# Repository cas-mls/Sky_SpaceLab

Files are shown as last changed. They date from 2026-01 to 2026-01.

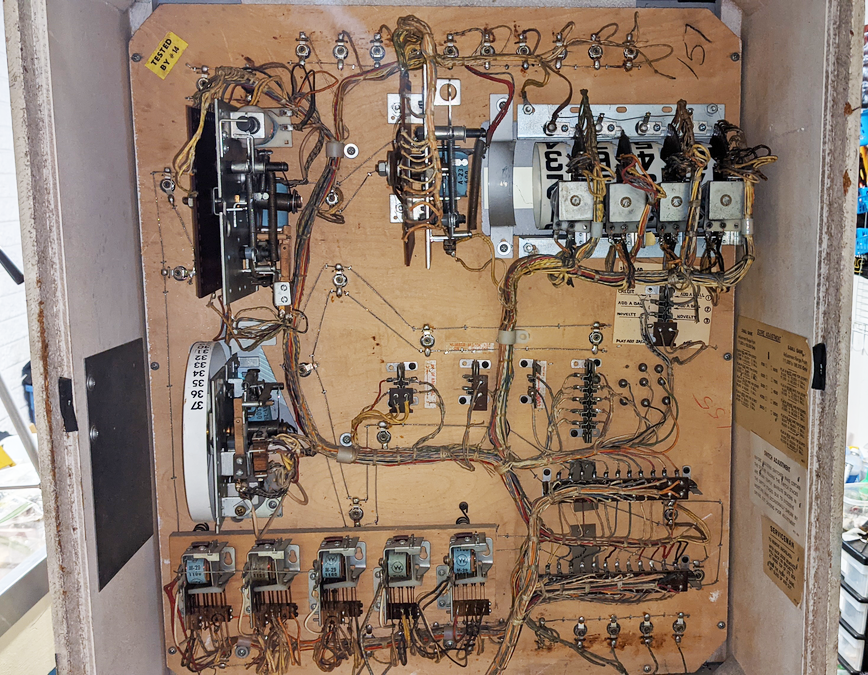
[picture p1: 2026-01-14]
BackCabinet1.png

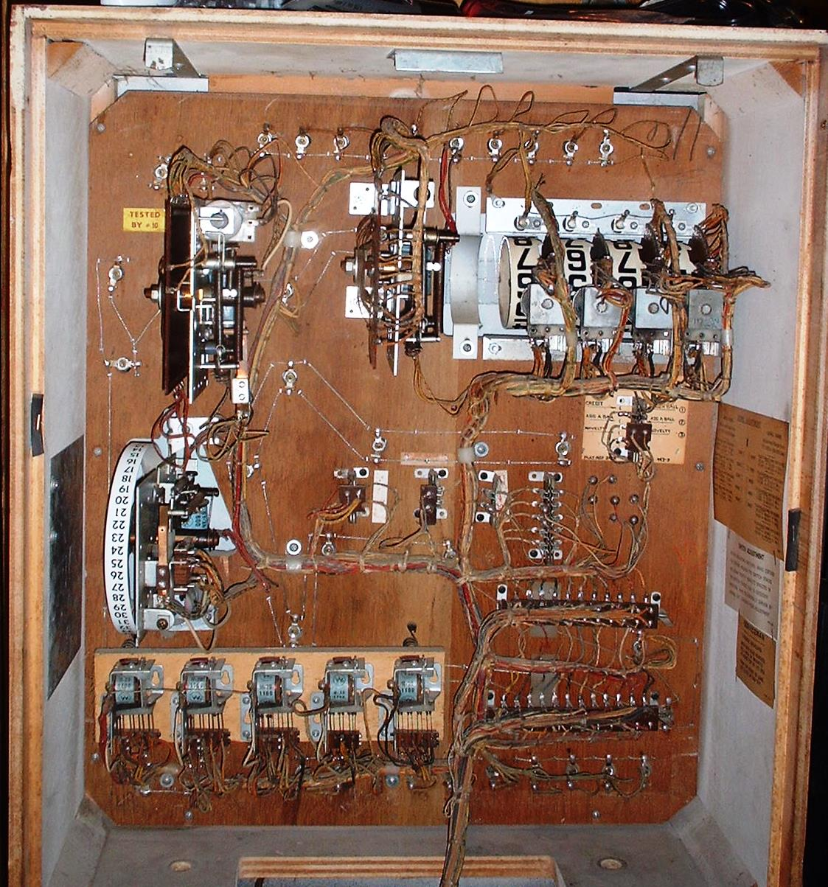
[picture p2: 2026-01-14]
BackCabinet.png

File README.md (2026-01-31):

# Space Lab Pinball (Williams)

## Spacelab/Skylab Links:

- [EM Repair](https://www.pinrepair.com/em/)
- [Pinside](https://pinside.com/pinball/machine/spacelab)
- [YouTube](https://www.youtube.com/watch?v=ZWouGSnXjZg)
- [Score Wheel](https://homepinballrepair.com/em-score-reels/#:~:text=Introduction,sensor%20switch%20is%20not%20working.)
- [IPDB Sky Lab](https://www.ipdb.org/machine.cgi?id=2202)
- [IPDB Space Lab](https://www.ipdb.org/machine.cgi?id=6620)
- [Williams 1974 Skylab  Instruction Manual](Williams_1974_Skylab_Instruction_Manual_Fixedup.pdf)
- [Williams 1977-1978 Parts Catalog](1977-1978williams.pdf)
- [Williams Introduction to Coin-Operated Amusement Games](Introduction_to_Coin_Operated_Amusement_Games_text.pdf)

## Annotated Files

* [Schematic](Williams_1974_Skylab_Schematic_submitted_by_Steve_Corley_Annotated.pdf)
* [Inside Cabinet](InsideCabinetAnnotated.png)
* [Back Cabinet](BackCabinetAnnotated.png)
* [Under Playfield](UnderPlayFieldAnnotated.png)

## Logic Simulation

* [Source Code](Skylab)

## Issues

* [Open Issues](https://github.com/cas-mls/Sky_SpaceLab/issues)
* [Closed Issues](https://github.com/cas-mls/Sky_SpaceLab/issues?q=is%3Aissue%20state%3Aclosed)

## Status:

## 16 -Jan-2026

* The 100 Point Drum is not resetting, and the score motor continues to run.
  * Fixed
    * Adjusted the Score Reset Relay Contacts.
    * Re-soldered a loose wire on the top, switched on the 100 Point Drum.
* Tilt Issue
  * Checked all of the Tilt switches.
    * Fixed
      * Not a consistent issue.
      * Found one that has insulation off and might be shorting with the other switch wire.
      * Found a Tilt Relay next to the score motor.  The front Slam and Kick sets this relay, and cannot be reset.
* Ball Count
  * The ball count adjustment is set to 5 balls.  The machine only shows 2 balls, but plays 3 balls.  Possible light bulb is burned out.
* 1000 Point Drum during reset?
  * When resetting with the credit button, or Reset Relay, maybe even when turning on.
    * This needs to be monitored.
    * It fixed itself after some time working on other issues.
    * During the reset, the first latched relay goes off and on, and the knocker is energized.
* Pressing the "S" and "K" causes the 10's drum to keep going and the Score Motor keep running.  Also, related to the 10's Drum is working if the rest of the "SKYLAB" is pressed, then the Advance Unit also runs, making a large racket.
  * Check the 50 Point Relay; it might not be shutting off. (Fixed Issue #4, Not sure if it is registering points.)
* Five balls in-line
  * Not sure if this is working correctly. (Wrote Issue #5)

## 21-Jan-2026

- Verify that the 1000 Point Continuous running has been fixed. (Close Issue #3).
- Verify that the 5 Balls In-Line is working (Close Issue #5)
- Fixed the 5-Ball Setting not working by cleaning up the Ball Stepper (Close Issue #6).
- SKYLAB causes the Score Motor to continue to work without stopping (Wrote Issue #13).
- Vacuum inside the machine; clean and wax the Playfield; clean contacts. Didn't find any lights to replace. (Issue #8)
- Playfield Inserts are loose and crooked (Wrote Issue #11)
- Right Flipper does not hold the ball.  Adjust the End of Stroke contact.  But look into rebuilding flippers. (Wrote Issue #12)
- Notice that loose legs cause the Tilt.  The research cost to fix the legs. (Wrote Issue #9)

## 30-Jan-2026

* Copied the Skylab Instruction Manual.

* Thought that this should be an easy problem, just adjust the Score Motor switch 5-C.  The 50 Point Relay, once turned on, stays on until the Score Motor cycles to the 5th position.  When the Score Motor cycles to the 50th position, the switch 5-C turns off, and the 50 Point Relay will turn off.

* Adjusted the 5-C Score Motor switch.  Managed to get the problem fixed, but the prior problem with the 50 Point Relay (Issue #4) returned.  Checked the workings of the Lock Switched on 50 Point Relay and the Skylab Relays, and verified that they worked.  Disable the Score Motor, verify that the relay turns off.  Turning on the Score Motor would cause the pinball to cycle correctly one or two times and then fail.

* Disable the Score Motor again and verify that the switch is disconnected and the relay is on.  Tapping on the relay causes it to shut.

* The problem with the pinball machine was that the Relay was stuck on.  With the pinball machine off, press the relay, and it would stick.  Cleaned the surface of the relay with sandpaper, and the Pinball Machine worked.  Which resolves Issue (#4 and #13).

* The triangle playfield inserts for the Rocket Special are warped.  Added the comment to Issue #11.

  ***Important Note: With the Score Motor OFF, the machine will register a TILT.***

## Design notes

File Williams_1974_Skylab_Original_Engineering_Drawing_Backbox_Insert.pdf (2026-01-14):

Original Backbox Insert Engineer Drawing for 1974 Williams Skylab Pinball! Backbox Insert Drawing for 1974 SKYLAB Pinball by Williams.
From the historic archives of Williams Pinball.
Original factory engineer drawing of the backbox insert for the single player game SKYLAB by Williams (model #443).
Hand drawn in pencil on mylar stock.

It is the actual size approx. 29" x 30".

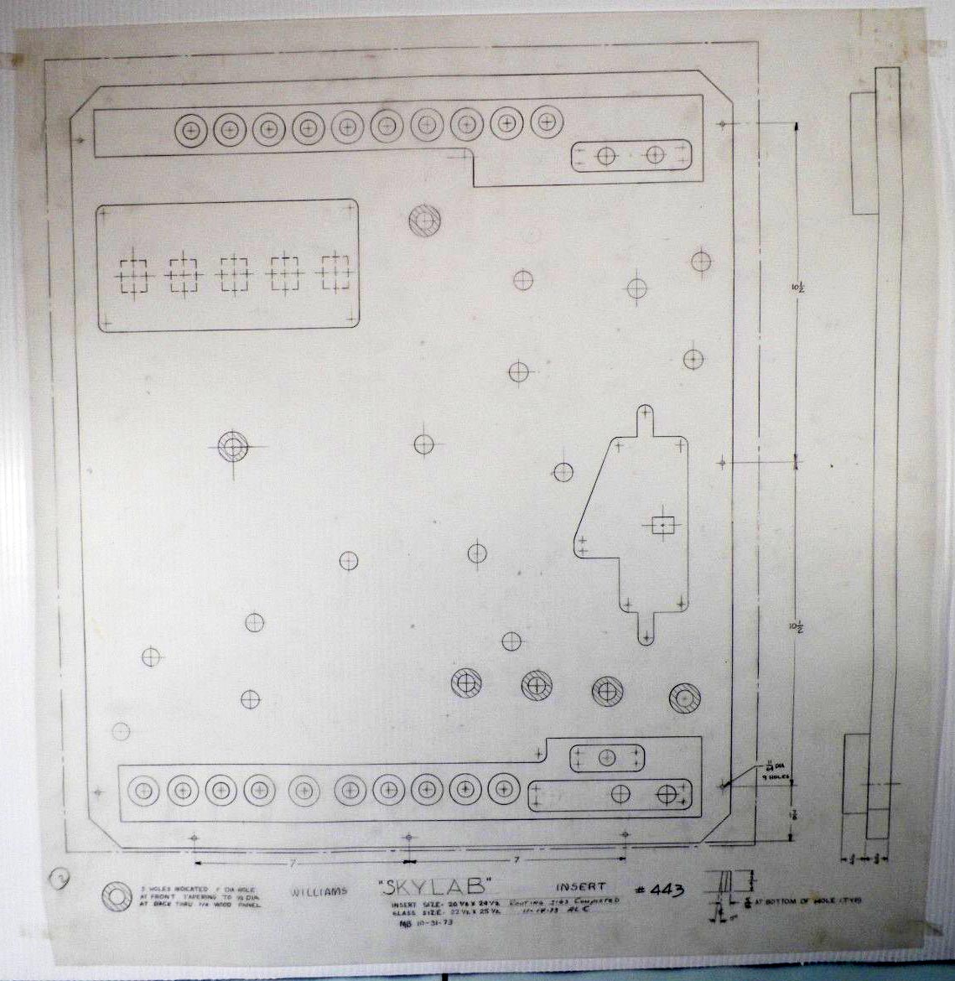
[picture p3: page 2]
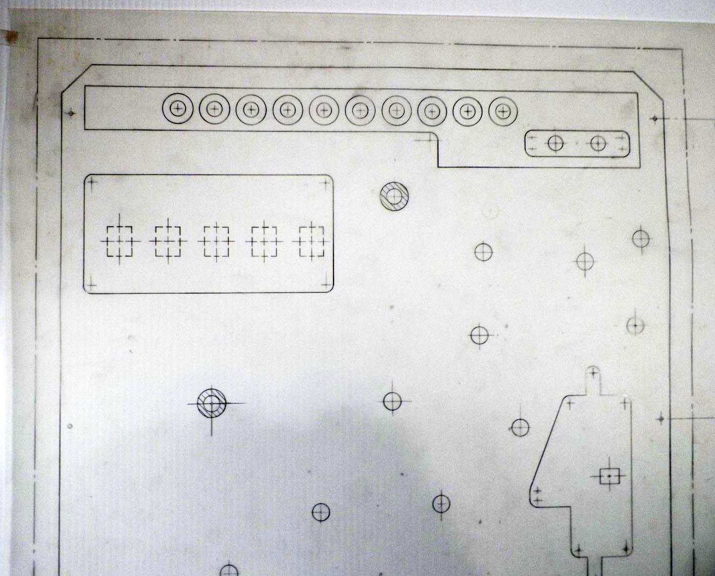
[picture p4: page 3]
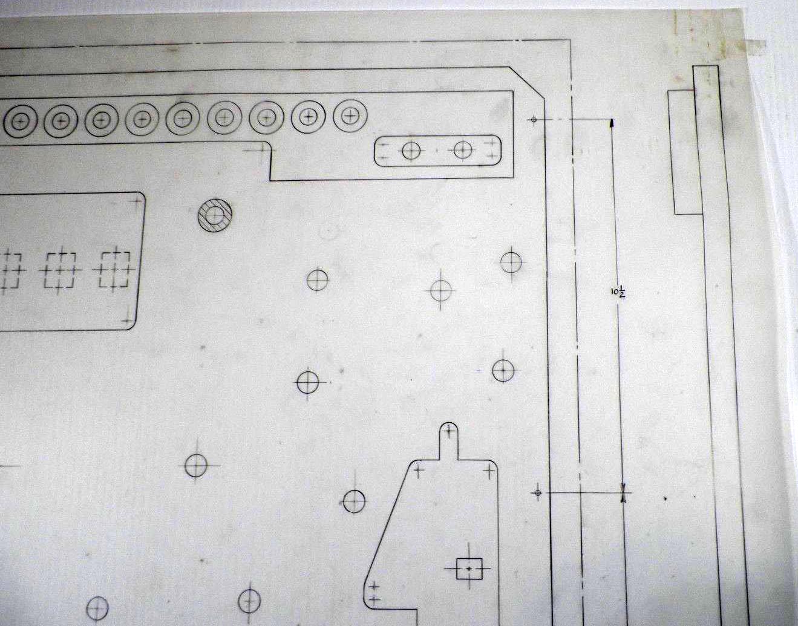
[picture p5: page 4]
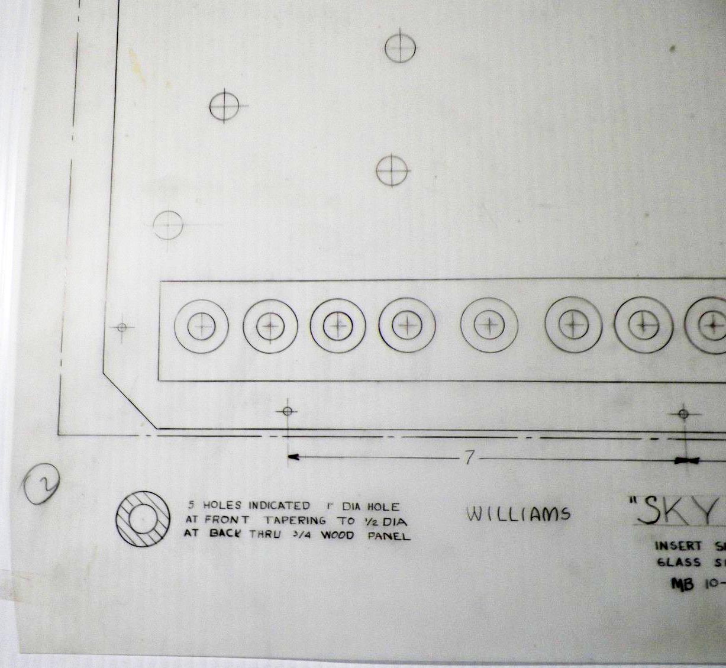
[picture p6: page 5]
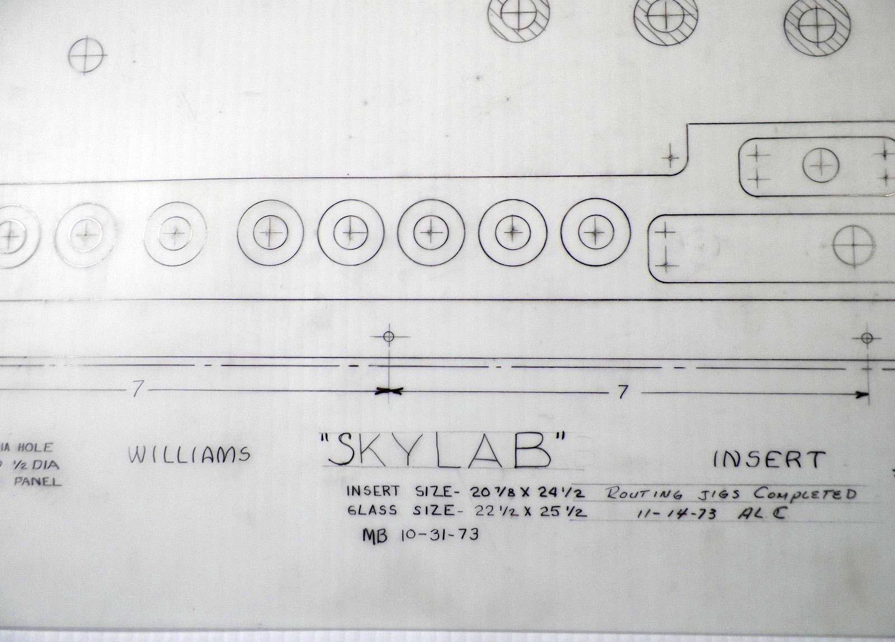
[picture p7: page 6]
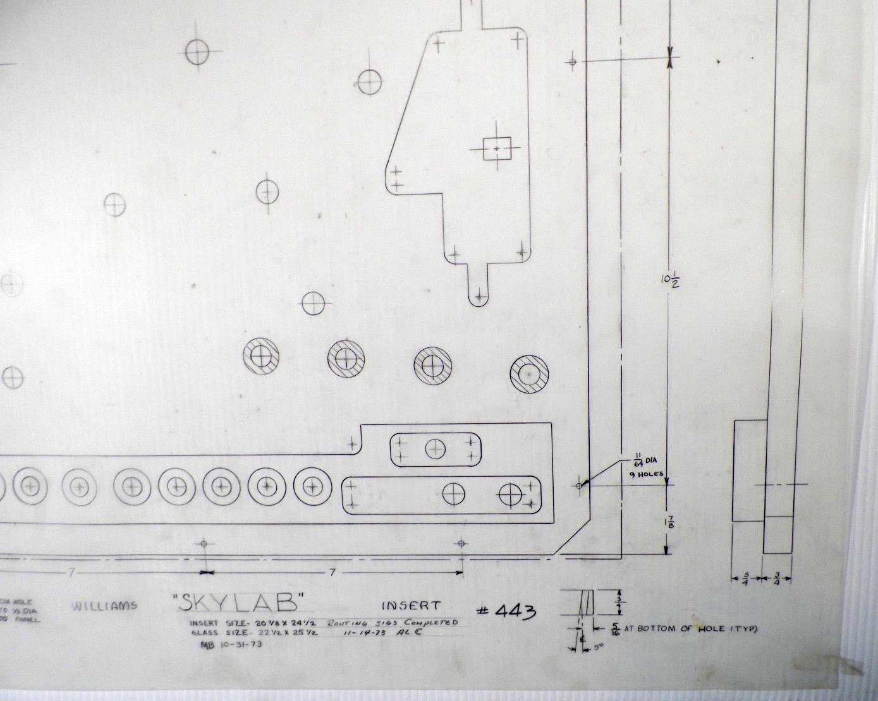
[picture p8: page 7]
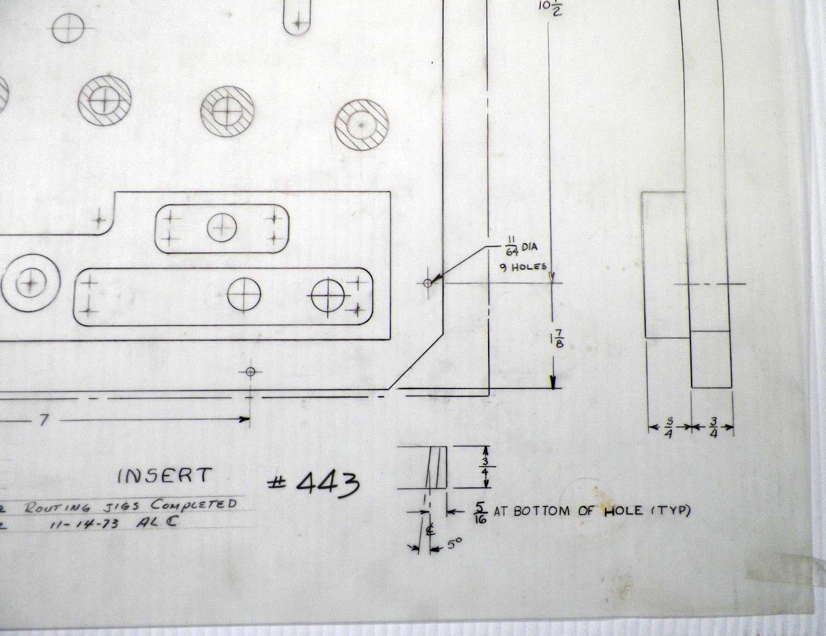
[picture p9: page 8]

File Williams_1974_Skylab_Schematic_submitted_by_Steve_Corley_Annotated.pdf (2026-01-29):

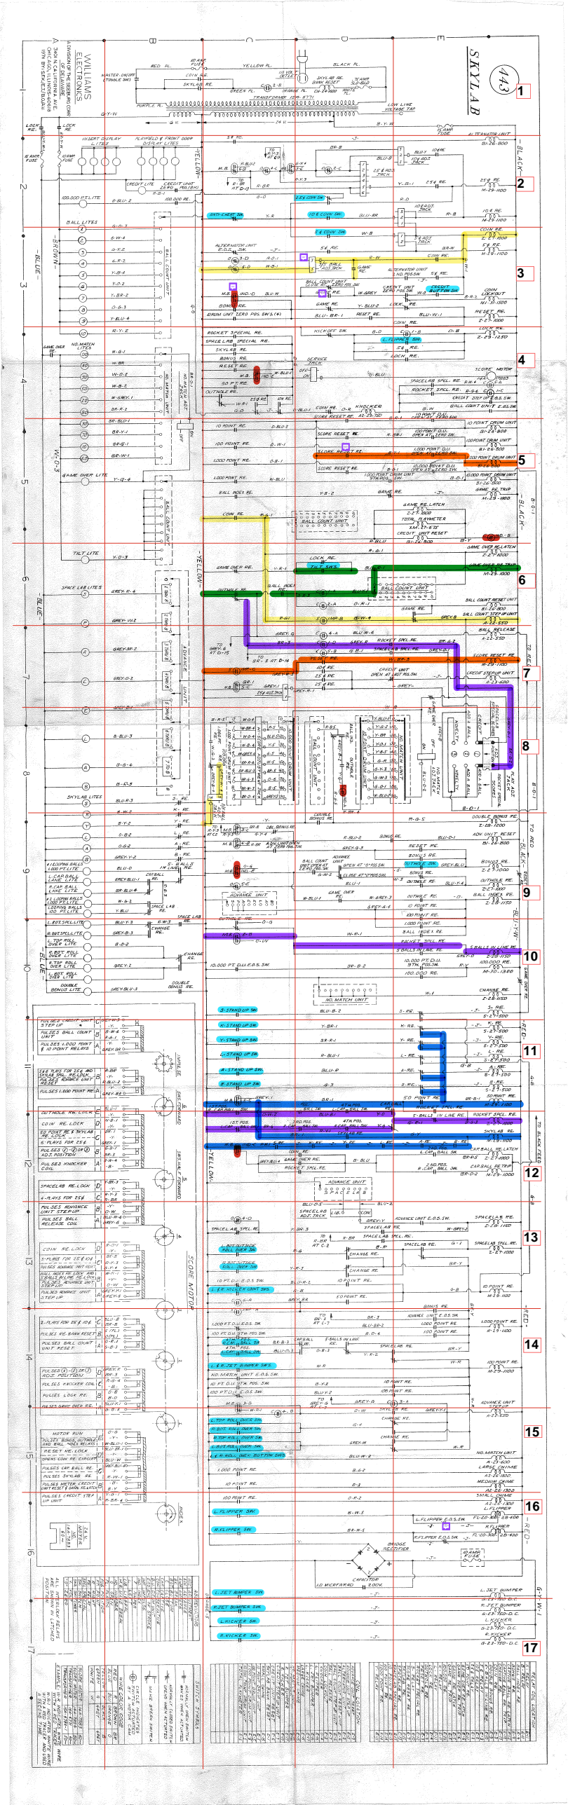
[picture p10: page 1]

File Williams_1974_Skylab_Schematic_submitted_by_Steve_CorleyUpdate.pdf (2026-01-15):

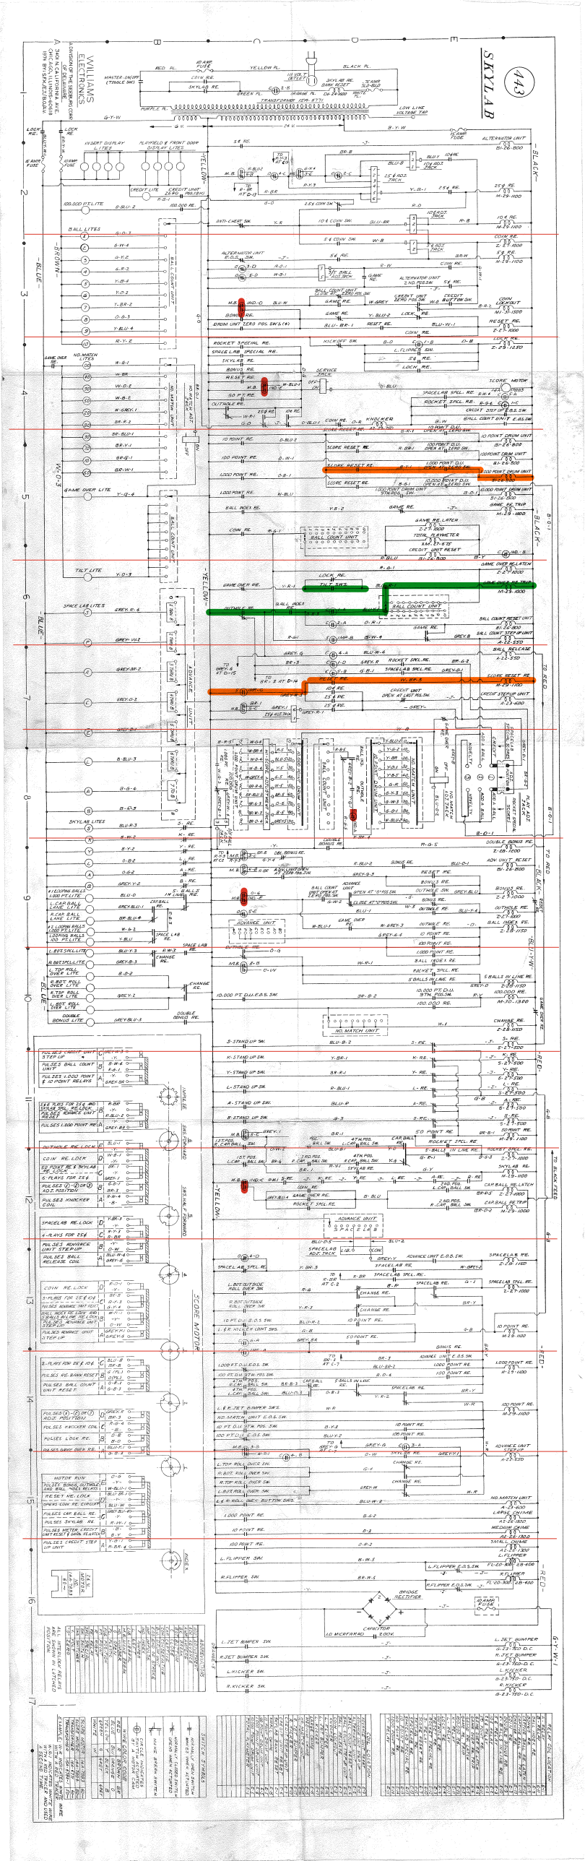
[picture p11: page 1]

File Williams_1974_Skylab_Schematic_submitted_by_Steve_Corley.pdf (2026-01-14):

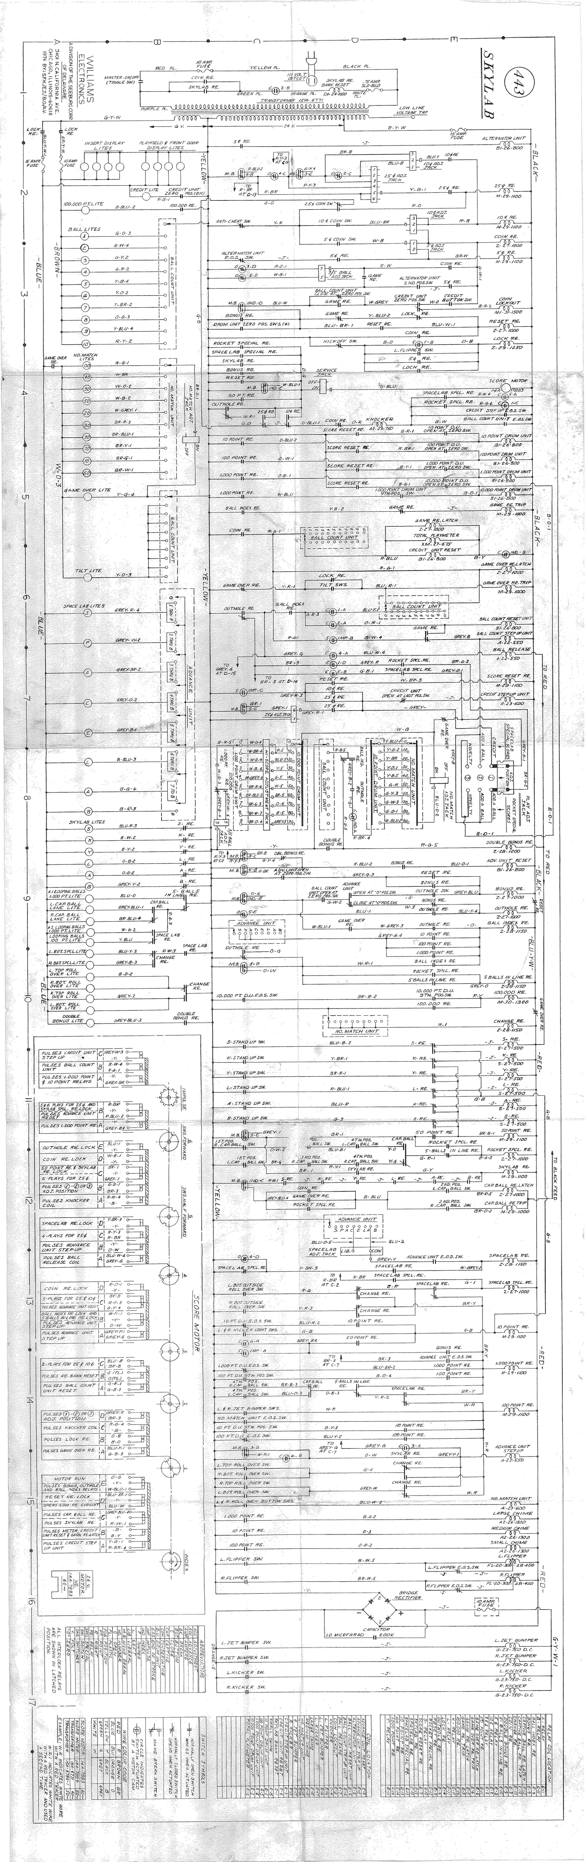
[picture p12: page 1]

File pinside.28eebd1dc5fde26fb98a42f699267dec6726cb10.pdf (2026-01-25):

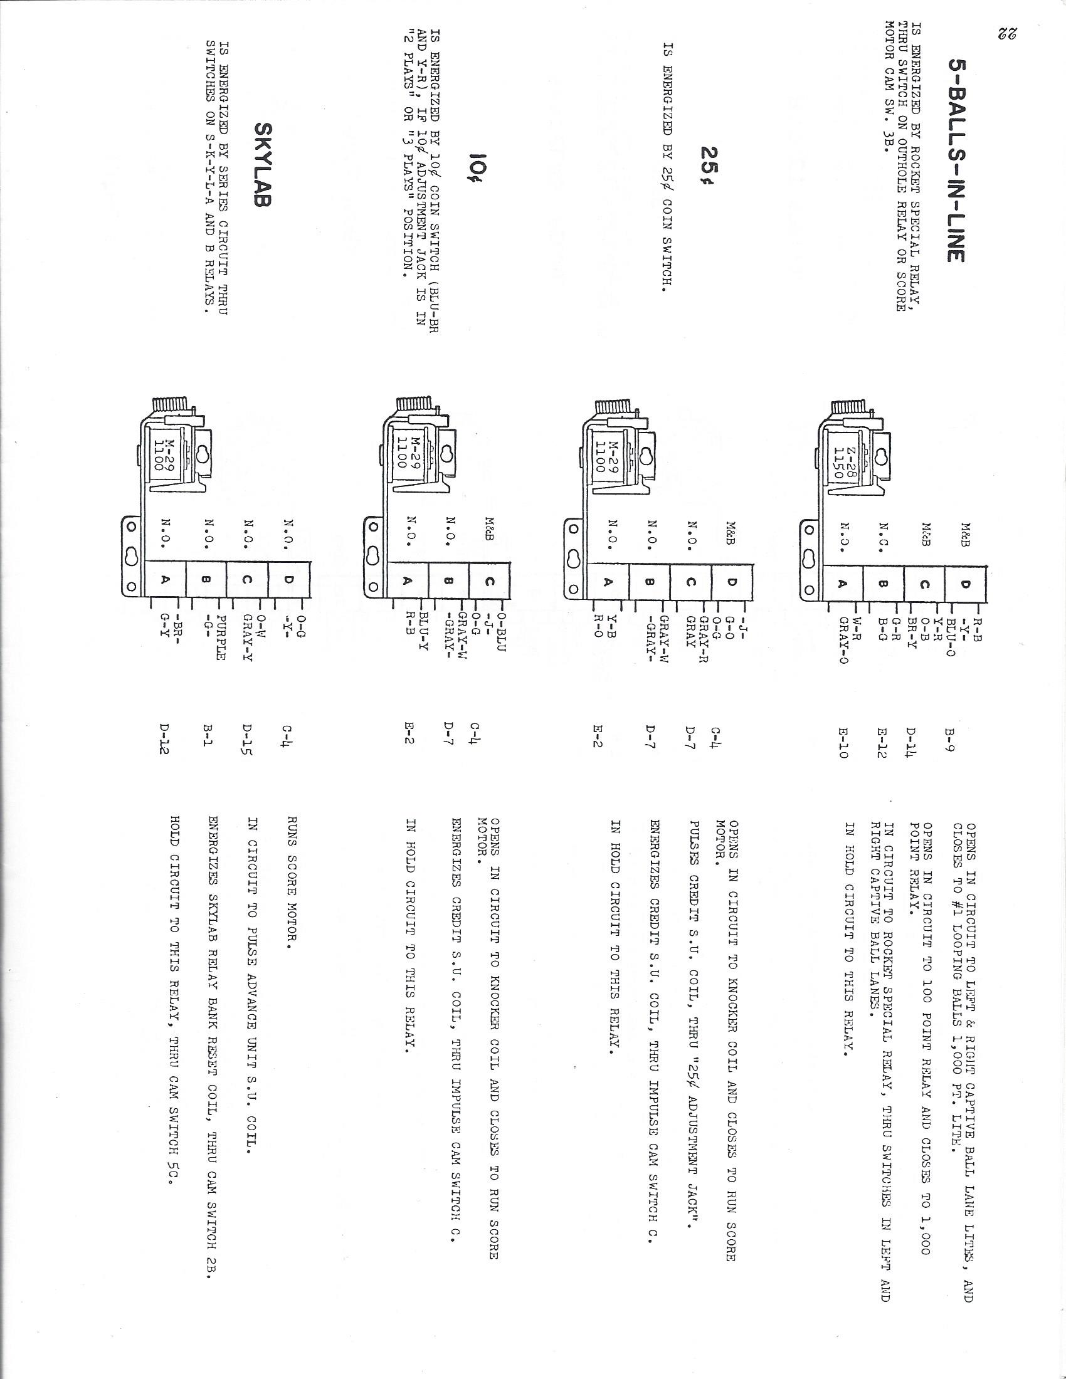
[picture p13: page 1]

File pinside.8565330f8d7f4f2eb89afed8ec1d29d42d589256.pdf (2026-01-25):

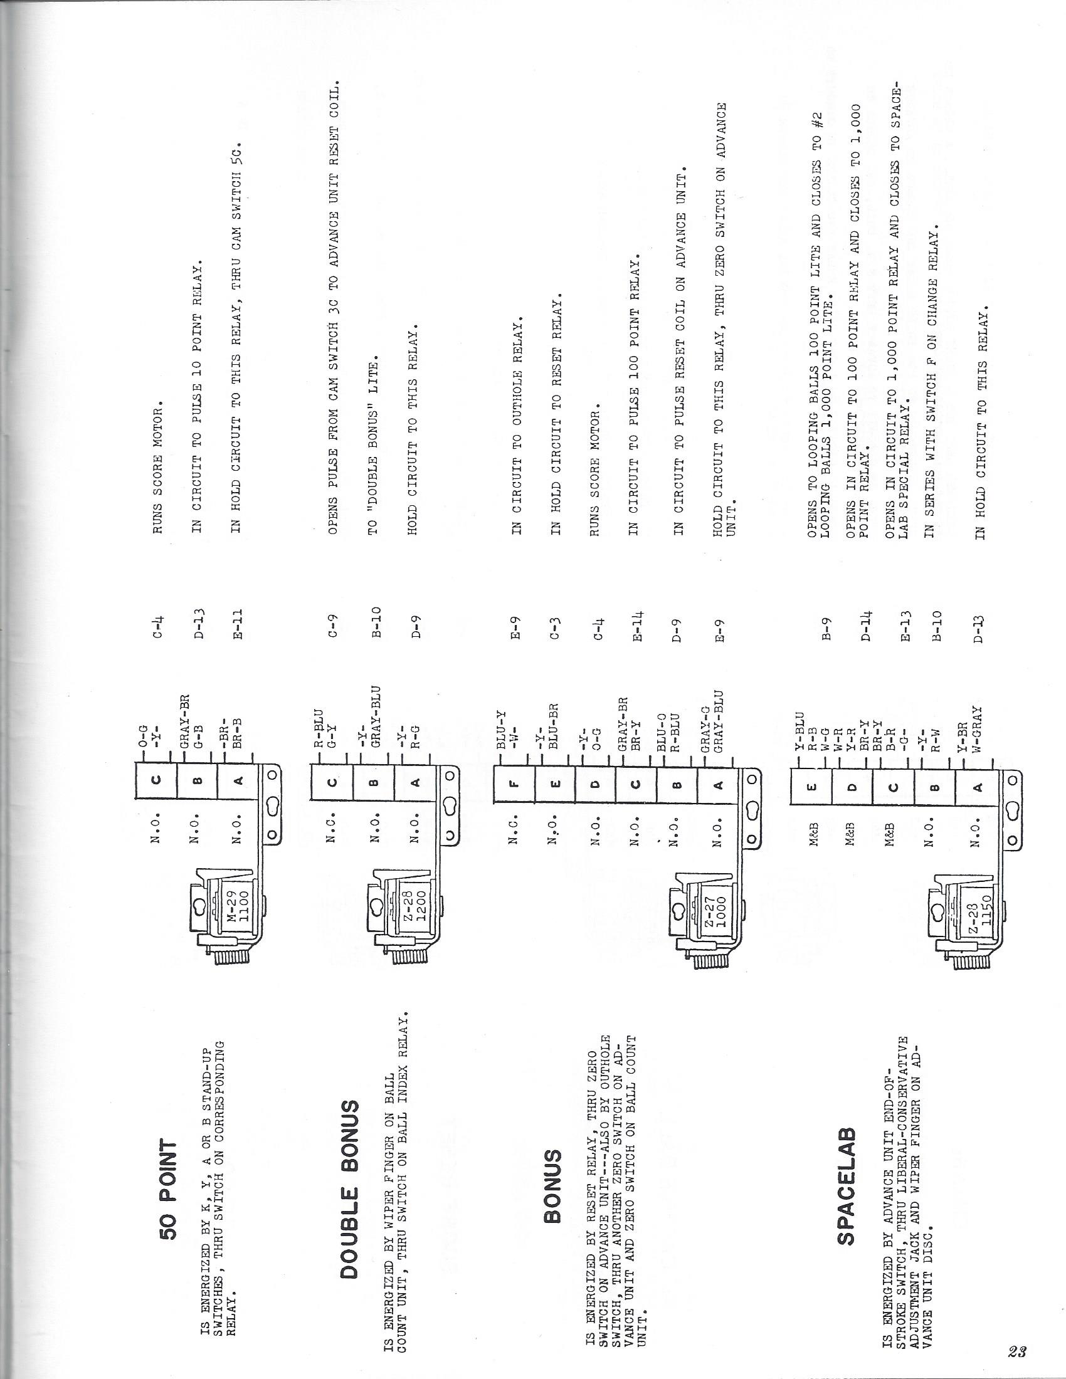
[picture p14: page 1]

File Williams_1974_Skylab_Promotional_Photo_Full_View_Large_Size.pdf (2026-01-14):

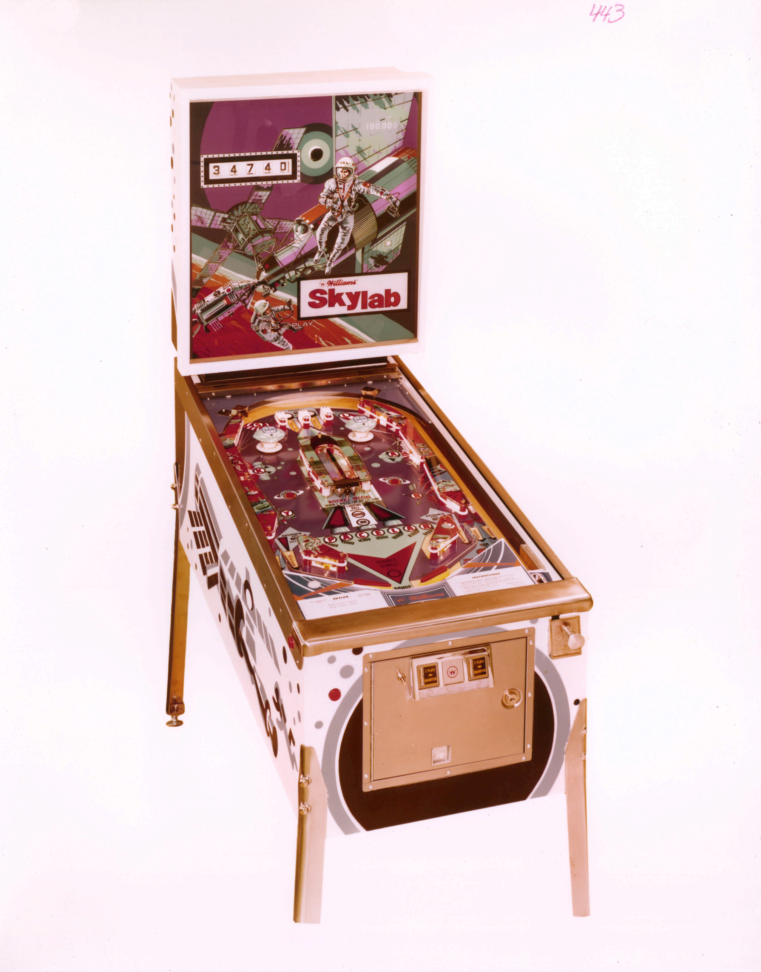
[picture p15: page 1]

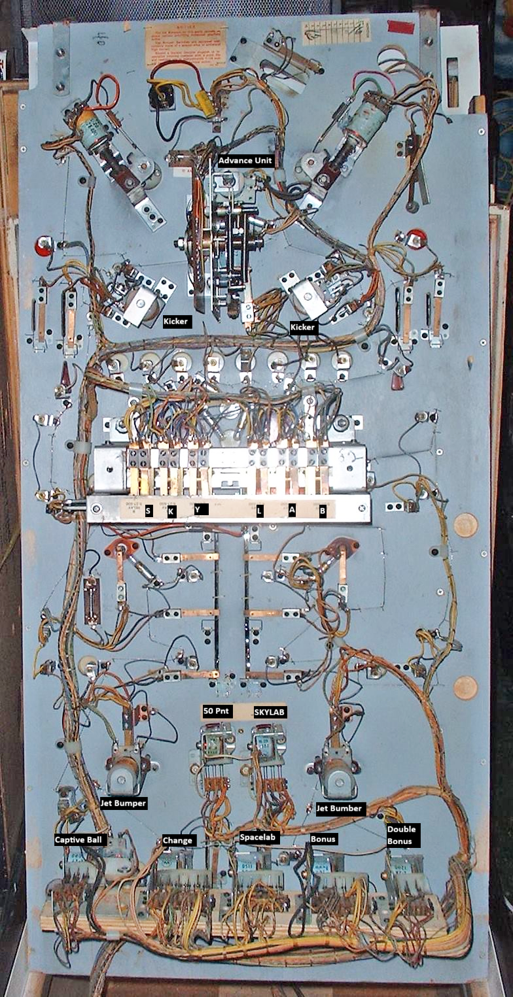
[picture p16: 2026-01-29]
UnderPlayFieldAnnotated.png

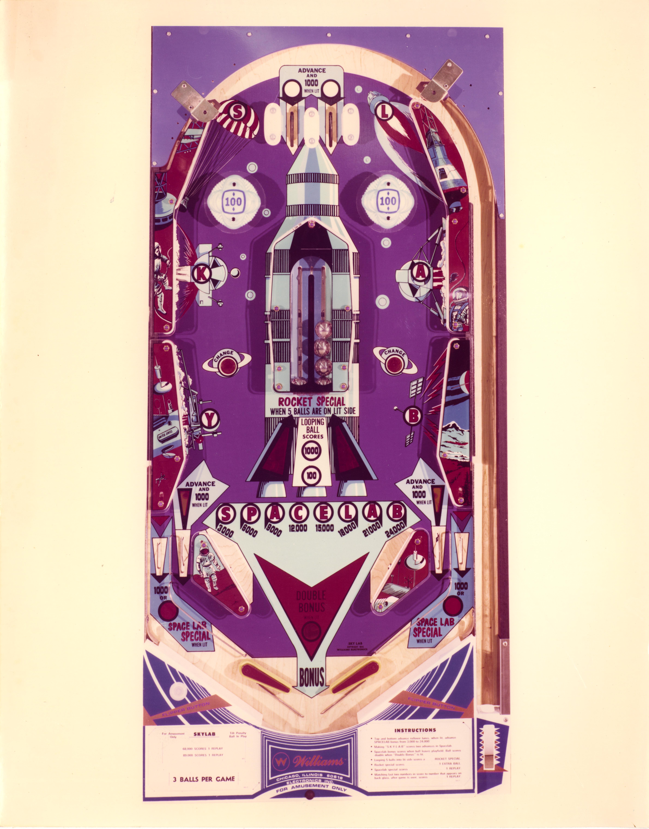
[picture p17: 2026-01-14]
Williams_1974_Skylab_Promotional_Photo_Playfield_Large_Size.jpg

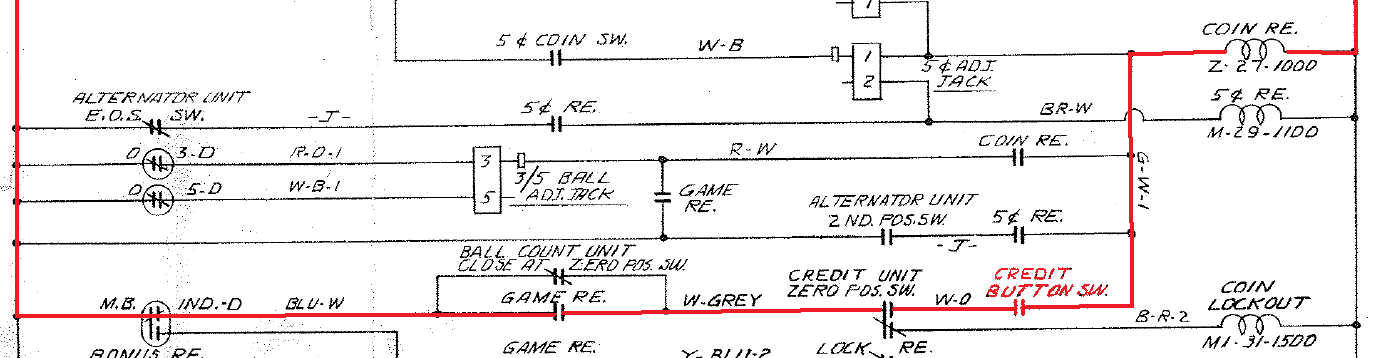
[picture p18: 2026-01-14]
CreditRelay.png

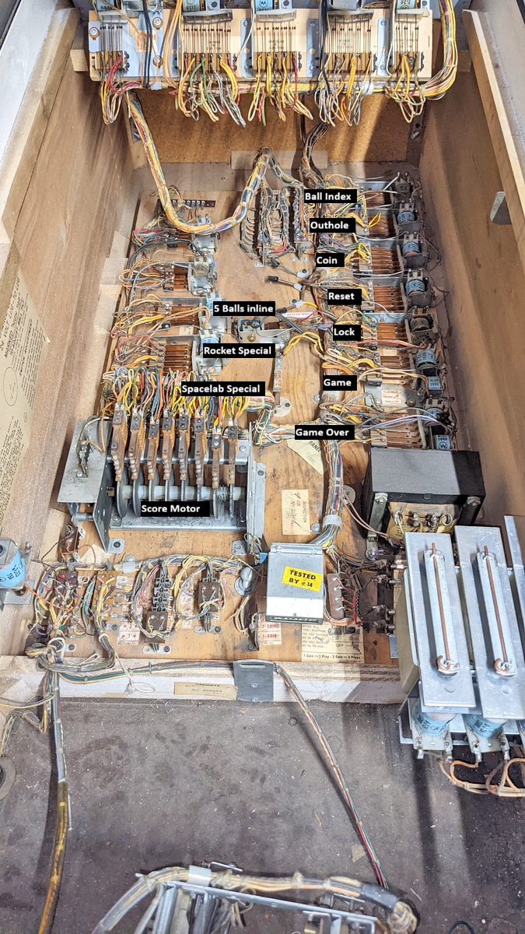
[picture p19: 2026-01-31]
InsideCabinetAnnotated.png

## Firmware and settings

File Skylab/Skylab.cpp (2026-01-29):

// Skylab.cpp : This file contains the 'main' function. Program execution begins and ends there.
//

#include <iostream>
#include <map>
#include <string>
#include <algorithm>

#include "StepperUnit.h"
#include "Relay.h"
#include "Solenoids.h"

int main()
{

    Solenoids::change = true;

    enum strictness {Liberal, Conservitive};

    // Adjustments
    int c25_adj = 5;
    int c10_adj = 1;
    int c5_adj = 2;
    int ball_3_5_adj = 5;
	int spacelabRocketSpecial_adj = 1;
	bool match_adj = false;
	strictness spaceLab_adj = Liberal;

    const int reA                 = 0;
    const int reB                 = 1;
    const int reBallIndex         = 2;
    const int reBonus             = 3;
    const int reCaptiveBall       = 4;
    const int reChange            = 5;
    const int reCoin              = 6;
    const int reDoubleBonus       = 7;
    const int reFiveBallInline    = 8;
    const int reC5                = 9;
    const int reC10               = 10;
    const int reC25               = 11;
    const int rePt50              = 12;
    const int reGameOver          = 13;
    const int reGame              = 14;
    const int rePt100000          = 15;
    const int reOutHole           = 16;
    const int reK                 = 17;
    const int reL                 = 18;
    const int reLock              = 19;
    const int reReset             = 20;
    const int reRocketSpecial     = 21;
    const int reS                 = 22;
    const int reScoreReset        = 23;
    const int reSkyLab            = 24;
    const int reSkylabBankReset   = 25;
    const int reSpaceLab          = 26;
    const int reSpaceLabSpecial   = 27;
    const int rePt10              = 28;
    const int rePt100             = 29;
    const int rePt1000            = 30;
    const int reY                 = 31;

    Relay re[reY + 1];

	re[reA] = Relay("a", Relay::RelayType);
	re[reB] = Relay("b", Relay::RelayType);
	re[reBallIndex] = Relay("ballIndex", Relay::RelayType);
	re[reBonus] = Relay("bonus", Relay::RelayType);
	re[reCaptiveBall] = Relay("captiveBall", Relay::RelayType);
	re[reChange] = Relay("change", Relay::RelayType);
	re[reCoin] = Relay("coin", Relay::RelayType);
	re[reDoubleBonus] = Relay("doubleBonus", Relay::RelayType);
	re[reFiveBallInline] = Relay("fiveBallInline", Relay::RelayType);
	re[reC5] = Relay("c5", Relay::RelayType);
	re[reC10] = Relay("c10", Relay::RelayType);
	re[reC25] = Relay("c25", Relay::RelayType);
	re[rePt50] = Relay("pt50", Relay::RelayType);
	re[reGameOver] = Relay("gameOver", Relay::RelayType);
	re[reGame] = Relay("game", Relay::RelayType);
	re[rePt100000] = Relay("pt100000", Relay::RelayType);
	re[reOutHole] = Relay("outHole", Relay::RelayType);
	re[reK] = Relay("k", Relay::RelayType);
	re[reL] = Relay("l", Relay::RelayType);
	re[reLock] = Relay("lock", Relay::RelayType);
	re[reReset] = Relay("reset", Relay::RelayType);
	re[reRocketSpecial] = Relay("rocketSpecial", Relay::RelayType);
	re[reS] = Relay("s", Relay::RelayType);
	re[reScoreReset] = Relay("scoreReset", Relay::RelayType);
	re[reSkyLab] = Relay("skyLab", Relay::RelayType);
	re[reSkylabBankReset] = Relay("skylabBankReset", Relay::RelayType);
	re[reSpaceLab] = Relay("spaceLab", Relay::RelayType);
	re[reSpaceLabSpecial] = Relay("spaceLabSpecial", Relay::RelayType);
	re[rePt10] = Relay("pt10", Relay::RelayType);
	re[rePt100] = Relay("pt100", Relay::RelayType);
	re[rePt1000] = Relay("pt1000", Relay::RelayType);
	re[reY] = Relay("y", Relay::RelayType);

    const int reSize = std::size(re);

    Relay reAs[reSize];

    for (int i=0; i < reSize; ++i)
    {
        reAs[i] = Relay(re[i]);
	}

    bool impulse = false;

    const int advanceCount  = 0;
    const int alternator    = 1;
    const int ballCount     = 2;
    const int noMatch       = 3;
    const int credit        = 4;
    const int pt10          = 5;
    const int pt100         = 6;
    const int pt1000        = 7;
    const int pt10000       = 8;
    const int scoreMotor    = 9;

    StepperUnit units[scoreMotor + 1];
	units[advanceCount] = StepperUnit("advanceCount", 9);
	units[alternator] = StepperUnit("alternator", 2);
	units[ballCount] = StepperUnit("ballCount", 5, StepperUnit::UpDown);
	units[noMatch] = StepperUnit("noMatch", 10, StepperUnit::Continuous);
	units[credit] = StepperUnit("credit", 9, StepperUnit::UpDown);
	units[pt10] = StepperUnit("pt10", 9, StepperUnit::Continuous);
	units[pt100] = StepperUnit("pt100", 9, StepperUnit::Continuous);
	units[pt1000] = StepperUnit("pt1000", 9, StepperUnit::Continuous);
	units[pt10000] = StepperUnit("pt10000", 9, StepperUnit::Continuous);
	units[scoreMotor] = StepperUnit("scoreMotor", 5, StepperUnit::Continuous);

    const int unitsSize = std::size(units);
    StepperUnit unitsA[unitsSize];
    for (int i = 0; i < unitsSize; ++i)
    {
        unitsA[i] = StepperUnit(units[i]);
    }

    // Alternator Unit
    int alternatorUnit = 0;             // E-2
    bool altUnit_eos = false;          // TODO: altUnit_eos - Don't know what value;

    // SkyLab Unit Stepper
    bool skyLabResetUnit = false;      // D-1

	const int solBallRelease = 0;
	const int solCoinLockout = 1;
	const int solKnocker = 2;
	const int solLeftFlipper = 3;
	const int solLeftJetBumper = 4;
	const int solLargeChime = 5;
	const int solMediumChime = 6;
	const int solSmallChime = 7;
	const int solTotalPaymeter = 8;

	Relay sol[solTotalPaymeter + 1];

	sol[solBallRelease] = Relay("ballRelease", Relay::Solenoid);
	sol[solCoinLockout] = Relay("coinLockout", Relay::Solenoid);
	sol[solKnocker] = Relay("knocker", Relay::Solenoid);
	sol[solLeftFlipper] = Relay("leftFlipper", Relay::Solenoid);
	sol[solLeftJetBumper] = Relay("leftJetBumper", Relay::Solenoid);
	sol[solLargeChime] = Relay("largeChime", Relay::Solenoid);
	sol[solMediumChime] = Relay("mediumChime", Relay::Solenoid);
	sol[solSmallChime] = Relay("smallChime", Relay::Solenoid);
	sol[solTotalPaymeter] = Relay("totalPaymeter", Relay::Solenoid);

	int solenoidsSize = std::size(sol);
	Relay priorSol[solTotalPaymeter + 1];

    // Switches
    const int tilt_sw               = 0;
    const int kickOff_sw            = 1;
    const int leftFlipper_sw        = 2; // C-16 (2)
    const int c25_sw                = 3;          // D-2
    const int c10_sw                = 4;          // D-2
    const int c5_sw                 = 5;           // D-3
    const int antiCheat_sw          = 6;    // C-2
    const int creditButton_sw       = 7; // E-3
	const int sStandup_sw           = 8;     // E-10
    const int kStandup_sw           = 9;     // E-11
    const int yStandup_sw           = 10;     // E-11
    const int lStandup_sw           = 11;     // E-11
    const int aStandup_sw           = 12;     // E-11
    const int bStandup_sw           = 13;     // E-11
    const int outHole_sw            = 14; // D-9
	const int right1CaptiveBall_sw  = 15; // D-12
	const int left1CaptiveBall_sw   = 16;  // D-12
    const int right2CaptiveBall_sw  = 17; // D-12
    const int left2CaptiveBall_sw   = 18;  // D-12
    const int right3CaptiveBall_sw  = 19; // D-12
    const int left3CaptiveBall_sw   = 20;  // D-12
    const int right4CaptiveBall_sw  = 21; // D-12
    const int left4CaptiveBall_sw   = 22;  // D-12
	const int leftBotOutsideRollover_sw = 23; // D-13
    const int rightBotOutsideRollover_sw = 24; // D-13
	const int leftKickerCount_sw    = 25; // D-13
	const int rightKickerCount_sw   = 26; // D-13
    const int leftJetBumper_sw      = 27; // E-14
	const int rightJetBumper_sw     = 28; // E-14
    const int rightTopRollover_sw   = 29; // E-15
    const int leftTopRollover_sw    = 30;  // E-15
    const int rightBottomRollover_sw = 31; // E-15
	const int leftBottomRollover_sw = 32;  // E-15
    const int leftRolloverButton_sw = 33; // E-16
    const int rightRolloverButton_sw = 34; // E-16

    Relay sw[rightRolloverButton_sw + 1];

	sw[tilt_sw] = Relay("tilt", Relay::Switch);
	sw[kickOff_sw] = Relay("kickOff", Relay::Switch);
	sw[leftFlipper_sw] = Relay("leftFlipper", Relay::Switch);
	sw[c25_sw] = Relay("c25", Relay::Switch);
	sw[c10_sw] = Relay("c10", Relay::Switch);
	sw[c5_sw] = Relay("c5", Relay::Switch);
	sw[antiCheat_sw] = Relay("antiCheat", Relay::Switch);
	sw[creditButton_sw] = Relay("creditButton", Relay::Switch);
	sw[sStandup_sw] = Relay("sStandup", Relay::Switch);
	sw[kStandup_sw] = Relay("kStandup", Relay::Switch);
	sw[yStandup_sw] = Relay("yStandup", Relay::Switch);
	sw[lStandup_sw] = Relay("lStandup", Relay::Switch);
	sw[aStandup_sw] = Relay("aStandup", Relay::Switch);
	sw[bStandup_sw] = Relay("bStandup", Relay::Switch);
	sw[outHole_sw] = Relay("outHole", Relay::Switch);
	sw[right1CaptiveBall_sw] = Relay("right1CaptiveBall", Relay::Switch);
	sw[left1CaptiveBall_sw] = Relay("left1CaptiveBall", Relay::Switch);
	sw[right2CaptiveBall_sw] = Relay("right2CaptiveBall", Relay::Switch);
	sw[left2CaptiveBall_sw] = Relay("left2CaptiveBall", Relay::Switch);
	sw[right3CaptiveBall_sw] = Relay("right3CaptiveBall", Relay::Switch);
	sw[left3CaptiveBall_sw] = Relay("left3CaptiveBall", Relay::Switch);
	sw[right4CaptiveBall_sw] = Relay("right4CaptiveBall", Relay::Switch);
	sw[left4CaptiveBall_sw] = Relay("left4CaptiveBall", Relay::Switch);
	sw[leftBotOutsideRollover_sw] = Relay("leftBotOutsideRollover", Relay::Switch);
	sw[rightBotOutsideRollover_sw] = Relay("rightBotOutsideRollover", Relay::Switch);
	sw[leftKickerCount_sw] = Relay("leftKickerCount", Relay::Switch);
	sw[rightKickerCount_sw] = Relay("rightKickerCount", Relay::Switch);
	sw[leftJetBumper_sw] = Relay("leftJetBumper", Relay::Switch);
	sw[rightJetBumper_sw] = Relay("rightJetBumper", Relay::Switch);
	sw[rightTopRollover_sw] = Relay("rightTopRollover", Relay::Switch);
	sw[leftTopRollover_sw] = Relay("leftTopRollover", Relay::Switch);
	sw[rightBottomRollover_sw] = Relay("rightBottomRollover", Relay::Switch);
	sw[leftBottomRollover_sw] = Relay("leftBottomRollover", Relay::Switch);
	sw[leftRolloverButton_sw] = Relay("leftRolloverButton", Relay::Switch);
	sw[rightRolloverButton_sw] = Relay("rightRolloverButton", Relay::Switch);

    const int swSize = std::size(sw);
	
    Relay priorSw[swSize];


    // Odd Items


	for (int step = 0; step < 100; ++step)
    {
		// Topic: !!!! Step Control
        std::cout << "***** step = " << step << "\n";

		// Set prior switch states
        for (int i = 0; i < swSize; ++i)
        {
            priorSw[i].Assign(sw[i]);
        }

        // Topic: Outhole Test
        //{
        //    if (step == 0)
        //    {
        //        // Sets the initial conditions machine power up and started.
        //        reAs[reLock] = true;
        //        reAs[reCoin] = false;
        //        reAs[reGame] = true;
        //        reAs[reGameOver] = false;
        //        reAs[reReset] = false;
        //        reAs[reScoreReset] = false;
        //        unitsA[ballCount] = 0;
        //        unitsA[credit] = 5;
        //    }
        //    if (step == 3)
        //    {
        //        sw[outHole_sw] = true; // D-9
        //        unitsA[ballCount] = 5;
        //    }
        //    if (step == 12)
        //        sw[outHole_sw] = false; // D-9
        //}

		// Topic: K Standup Test
   //     {
   //         if (step == 0)
   //         {
   //             // Sets the initial conditions machine power up and started.
   //             reAs[reLock] = true;
   //             reAs[reCoin] = false;
   //             reAs[reGame] = true;
   //             reAs[reGameOver] = false;
   //             reAs[reReset] = false;
   //             reAs[reScoreReset] = false;
   //             unitsA[ballCount] = 0;
   //             unitsA[credit] = 5;
   //         }
   //         if (step == 3)
   //         {
   //             sw[kStandup_sw] = true;          // D-2
   //         }
   //         if (step == 5)
   //         {
   //             sw[kStandup_sw] = false;          // D-2
			//}

   //     }
        
        // Topic: SKYLAB Tests
        {
            if (step == 0)
            {
                // Sets the initial conditions machine power up and started.
                reAs[reLock] = true;
                reAs[reCoin] = false;
                reAs[reGame] = true;
                reAs[reGameOver] = false;
                reAs[reReset] = false;
                reAs[reScoreReset] = false;
                unitsA[ballCount] = 0;
                unitsA[credit] = 5;
            }
            if (step == 3)
            {
                sw[kStandup_sw]             = true;          // D-2
                sw[yStandup_sw]             = true;          // D-2
                sw[lStandup_sw]             = true;          // D-2
                sw[aStandup_sw]             = true;          // D-2
                sw[bStandup_sw]             = true;          // D-2
            }
            if (step == 5)
            {
                sw[kStandup_sw]             = false;          // D-2
                sw[yStandup_sw]             = false;          // D-2
                sw[lStandup_sw]             = false;          // D-2
                sw[aStandup_sw]             = false;          // D-2
                sw[bStandup_sw]             = false;          // D-2
            }
            if (step == 20)
            {
                sw[sStandup_sw] = true;          // D-2
            }
            if (step == 21)
            {
                sw[sStandup_sw] = false;          // D-2
            }
        }



            //sw[creditButton_sw] = true;          // E-3
            //sw[leftKickerCount_sw]      = true; // D-13
            //sw[rightKickerCount_sw]     = true; // D-13
            //sw[leftJetBumper_sw]        = true; // E-14
            //sw[rightJetBumper_sw]       = true; // E-14
            //sw[leftTopRollover_sw] = true;  // E-15  *****
            //sw[rightBottomRollover_sw]  = true; // E-15
            //sw[rightTopRollover_sw]     = true; // E-15
            //sw[leftBottomRollover_sw]   = true;  // E-15
            //sw[leftRolloverButton_sw]   = true; // E-16
            //sw[rightRolloverButton_sw]  = true; // E-16
        //}
        //if (step == 5)
        //{
			//sw[creditButton_sw] = false;          // E-3
            //sw[leftKickerCount_sw]      = false; // D-13
            //sw[rightKickerCount_sw]     = false; // D-13
            //sw[leftJetBumper_sw]        = false; // E-14
            //sw[rightJetBumper_sw]       = false; // E-14
            //sw[leftTopRollover_sw]      = false;  // E-15 *****
            //sw[rightBottomRollover_sw]  = false; // E-15
            //sw[rightTopRollover_sw]     = false; // E-15
            //sw[leftBottomRollover_sw]   = false;  // E-15
            //sw[leftRolloverButton_sw]   = false; // E-16
            //sw[rightRolloverButton_sw]  = false; // E-16
        //}
        //if (step == 7)
        //    sw[rightBottomRollover_sw] = true; // E-15
        //if (step == 9)
        //    sw[rightBottomRollover_sw] = false; // E-15

        //    sw[rightBottomRollover_sw] = true; // E-15

        //if (step == 15)
        //    sw[outHole_sw] = true; // D-9

        //    sw[rightBottomRollover_sw] = false; // E-15
        //if (step == 17)
        //    sw[outHole_sw] = false; // D-9
        //    sw[rightBottomRollover_sw] = true; // E-15

        
        //    sw[rightBottomRollover_sw] = false; // E-15
        //if (step == 19)
        //    sw[rightBottomRollover_sw] = true; // E-15
        //if (step == 21)
        //    sw[rightBottomRollover_sw] = false; // E-15
        //if (step == 25)
        //    sw[outHole_sw] = true;
        //if (step == 23)
        //    sw[rightBottomRollover_sw] = true; // E-15
        //if (step == 25)
        //    sw[rightBottomRollover_sw] = false; // E-15
        //if (step == 27)
        //    sw[rightBottomRollover_sw] = true; // E-15
        //if (step == 29)
        //    sw[rightBottomRollover_sw] = false; // E-15
        //if (step == 31)
        //    sw[rightBottomRollover_sw] = true; // E-15
        //if (step == 33)
        //    sw[rightBottomRollover_sw] = false; // E-15



        if (step == 20)
        {
            //sw[sStandup_sw] = true;          // D-2
        }
        if (step == 22)
        {
            //sw[sStandup_sw] = false;          // D-2
        }

        
        // Load previous assigned state
        for (int i=0; i < unitsSize; ++i)
        {
            units[i].Assign(unitsA[i]);
			unitsA[i].AssignEos(units[i]); // Update the eos
		}

        for (int i = 0; i < reSize; ++i)
        {
            re[i].Assign(reAs[i]);
		}
		for (int i = 0; i < solenoidsSize; ++i)
		{
			priorSol[i].Assign(sol[i]);
		}


            // Section 2
            // Alternator Unit Logic
    //        if (re[c5] && !c5_re_last)
    //        {
    //            alternatorUnit = alternatorUnit == 0 ? 1 : 0;
				//if (settle == 0) altUnit_eos = true;
    //            
    //        }
    //        if (settle == 0 && altUnit_eos) altUnit_eos = false;


        // Topic: 25 Cent Logic
        bool r_br = units[scoreMotor] != 6;
        bool r_y_3 = units[scoreMotor] != 4 && r_br;
        bool br_b = units[scoreMotor] != 3 && r_y_3;
        bool blu_b = units[scoreMotor] != 2 && br_b;
        bool y_b_1 = false;

        switch (c25_adj) {
        case 2:
            y_b_1 = blu_b;
            break;
        case 3:
            y_b_1 = br_b;
            break;
        case 4:
            y_b_1 = r_y_3;
            break;
        case 5:
            y_b_1 = r_br;
            break;
        default:
            y_b_1 = false;
            break;
        }
        bool r_o = !sw[antiCheat_sw] && sw[c25_sw];
        bool g_o = !sw[antiCheat_sw] && !sw[c25_sw]; // used in Section 4
        reAs[reC25] = (re[reC25] && y_b_1) || r_o;

        // Topic: 10 Cent Logic
        bool blu_y = false;
        switch (c10_adj) {
        case 2:
            blu_y = blu_b;
            break;
        case 3:
            blu_y = br_b;
            break;
        default:
            blu_y = false;
            break;
        }
        bool r_b = blu_y && re[reC10];

        bool blu_br = !sw[antiCheat_sw] && sw[c10_sw];
        switch (c10_adj) {
        case 2:
        case 3:
            reAs[reC10] = blu_br || r_b;
            break;
        default:
            reAs[reC10] = false;
            break;
        }

        // Section 3
        // Topic: Coin Relay Logic
        bool w_b = !sw[antiCheat_sw]
            && sw[c5_sw];
        bool g_w_1 = (w_b && (c5_adj == 1));
        g_w_1 = g_w_1 || blu_br && (c10_adj == 1);
        bool r_w = (units[scoreMotor] != 3 && ball_3_5_adj == 3)
            || (units[scoreMotor] != 5 && ball_3_5_adj == 5)
            /* || re[game]*/;
        g_w_1 = g_w_1 || (r_w && re[reCoin]);
        g_w_1 = g_w_1 || (alternatorUnit == 2 && re[reC5]);
        bool w_grey = /*scoreMotor != 0*/units[scoreMotor] == 0
            && (units[ballCount] == 0 || re[reGame]);
        g_w_1 = g_w_1 || w_grey
            && (units[credit] != 0
                && sw[creditButton_sw]);
        bool coin_re = w_b || g_w_1;
        reAs[reCoin] = w_b || g_w_1;

        // Topic: 5 Cent Logic
        reAs[reC5] = (altUnit_eos && re[reC5])
            || (c5_adj == 2 && w_b);

        // Topic: Coin Lockout Solenoid Logic
        sol[solCoinLockout] = (units[credit] == 0) && w_grey;

        // Topic: Reset Relay Logic
        int tmp = units[scoreMotor];
        bool blu_br_1 = re[reBonus] || /*(scoreMotor == 0) */ (units[scoreMotor] != 0);
        blu_br_1 = blu_br_1
            || (units[pt10] != 0 && units[pt100] != 0 && units[pt1000] != 0 && units[pt10000] != 0);
        bool y_blu_2 = blu_br_1 && (!re[reGame] && !re[reLock]);
        bool blu_w_1 = blu_br_1 && re[reReset];
        bool reset_re = y_blu_2 || blu_w_1 || re[reCoin];
        reAs[reReset] = y_blu_2 || blu_w_1 || re[reCoin];

        // Section 4
        // Topic: Lock Relay Logic
        reAs[reLock] = !sw[kickOff_sw]
            && (units[scoreMotor] == 1
                || sw[leftFlipper_sw]
                || re[reC5]
                || re[reLock]);

        // Topic: Score Motor Advance Logic
        //bool r_b_2 = re[coin] && !impulse;
        //bool br_b_1 = leftFlipper_sw && !impulse;
        //scoreMotor += (r_b_2 || br_b_1) ? 1 : 0;
        //scoreMotor = (scoreMotor > 6) ? 0 : scoreMotor;

        if (!impulse)
        {
                // Score Motor Logic
            if (re[reRocketSpecial]
                || re[reSpaceLabSpecial]
                || re[reSkyLab]
                || re[reBonus]
                || re[reReset]
                || units[scoreMotor] != 0
                || re[rePt50]
                || re[reOutHole]
                || (g_o && re[reC10])
                || (g_o && re[reC25]))
            {
                unitsA[scoreMotor]++;
                impulse = true;
            }
        }
        else
        {
            impulse = false;
        }

        // Topic: Knocker Solenoid Logic
        bool o_r = g_o && !re[reC25] && !re[reC10] && !re[reCoin];
        bool b_w = re[reSpaceLabSpecial] && units[scoreMotor] == 5
            || re[reRocketSpecial] && units[scoreMotor] == 1
            || units[credit].eos()
            || units[ballCount].eos();
        sol[solKnocker] = o_r && b_w;

        //Section 5
        // Topic: Score Drum Units Logic
        if (re[rePt10] || (re[reScoreReset] && units[pt10] != 0))
        {
            unitsA[pt10]++;
        }

        if (re[rePt100] || (re[reScoreReset] && units[pt100] != 0))
        {
            unitsA[pt100]++;
        }

        if (re[rePt1000] || (re[reScoreReset] && units[pt1000] != 0))
        {
            unitsA[pt1000]++;
        }

        bool b_o_1 = (re[reScoreReset] && units[pt10000] != 0);
        if (b_o_1 || units[pt1000] == 9000)
        {
            unitsA[pt10000]++;
        }
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

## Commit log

2026-01-18 Update with work performed on 16-jan-2026 Annotated files. Issues: Research 10 Pt running. Research 5-ball inline. Research 5-ball selector.
    [Logicschematic.kicad_pcb, Logicschematic.kicad_sch]
2026-01-21 Update schema for changes for 21-jan-2026 work. Update code to use classes for relay, steppers, solenoids.
2026-01-21 Add additional 50pt relay highlight
2026-01-25 Stop working on startup and manage to get most game play working. Added an Index spreadsheet.
    [ComponentIndex.xlsx]
2026-01-29 Updated software to make the relays, units, etc., from std::map to basic arrays. The individual devices are constants entries in the array. Updated the Schematic with vertical lines to separate the s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
    [ComponentIndex.xlsx, Logicschematic.kicad_sch]
